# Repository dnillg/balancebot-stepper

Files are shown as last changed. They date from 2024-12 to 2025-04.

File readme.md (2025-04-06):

# Stepper Balance Robot 

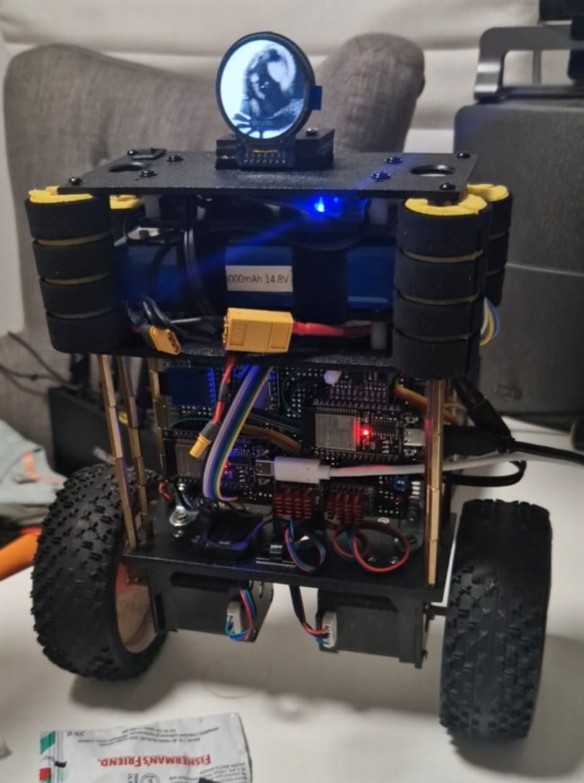
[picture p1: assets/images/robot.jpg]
Robot


## Description
A shoebox sized robot that can balance on two wheels. It uses a PID controller to maintain its balance and can be controlled over Bluetooth via an Android app.
It uses an ESP32 microcontroller, BNO085 IMU, two TMC5160T motor drivers, and two NEMA17 (~1.5A) stepper motors.
The robot is powered by a 3-4S LiPo battery and the chassis consists of metal spacers and 3-4mm PLA sheets.

Apart from the usual components, it has a 240x240 round LCD display and speaker driven by DFPlayer Mini MP3 module.

## Setting up for Development
1. Install VSCode and the PlatformIO extension.
2. Open one of the PlatformIO projects in VSCode (has platformio.ini in root).
3. Install Android Studio
4. Open the client app in Android Studio and run it on your phone.

## Architecture

### Control ESP32
- The ESP32 is the main controller of the robot. 
- It runs the PID controller and communicates with the motor drivers (SPI) and IMU (i2c).
- It has a HardwareSerial connection to the IO-ESP32.
- Control frequency is 200Hz.

### IO ESP32
- The IO ESP32 is responsible for the Bluetooth communication with the Android app.
- It has a HardwareSerial connection to the Control ESP32.
- It is connected to the LCD display (SPI), DFPlayer Mini (Software Serial), SD card module (SPI), and the other ESP32 (Hardware Serial).
- It receives commands from the Android app and sends them to the Control ESP32.
- It also processes the relevant commands.
- It can play sounds and display messages on the LCD with 15+ modes.

## Control / Balance Algorithm
- Cascade PID controller
- The current speed is calculated by the rolling average of the last 500ms
- Speed PID calculates a target roll angle
- Roll PID calculates the target speed of the motors
- The control input applies a difference to the target speed on each motor
- The Stepper motor has a maximum acceleration of ~10000-20000 steps/s², therefore the control output is dampened.
- The control output is limited to 8000 steps/s (Micro stepping: 16)

## Features
- Bluetooth control via Android app
- Diagnostic data streaming and rendering on the app (target roll angle, current roll angle, target speed, current speed, motor speed)
- PID tuning via Android app
- Displaying GIFs on LCD and Sound effects via DFPlayer Mini
- Balancing, driving, and turning

## Planned Features
- Battery feedback and monitoring
- Using a phone game controller Joystick for control

## Bill of Materials
| Component | Quantity | Description |
|---|---|---|
| ESP32 | 2 | 30 pin |
| BNO085 | 1 | IMU |
| TMC5160T | 2 | Motor driver |
| NEMA17 | 2 | Stepper motor, between 1.5A-2.1A nominal current |
| LiPo battery | 1 | 3-4S, 2200-30000mAh |
| LCD | 1 | 240x240 round LCD display |
| Speaker | 1 | 8 ohm, 0.5W-2W |
| DFPlayer Mini | 1 | MP3 module |
| Micro-SD card module | 1 | Micro-SD card module |
| Metal spacer 25mm | 16 | M3 metal spacer for the lower section |
| Metal spacer 20mm | 12 | M3 metal spacer for the upper section |
| 3mm PLA sheet | 2 | 150x65 (2), 35x100 (2) |
| 4mm PLA sheet | 1 | 150x65 |
| NEMA17 mount | 2 | Metal 90 degree bracket for NEMA17 motor |
| M3 screws | ? | 6mm-16mm |
| M3 nuts | ? | M3 nuts |
| Plastic spacer 15mm | 9 | M3 plastic spacer for the upper section |
| 120x80 double PCB | 1 | Double sided prototype PCB |
| XT30 connector | 2 | XT30 connector for power connection |
| XT60 connector | 1 | XT60 connector for power connection |
| 2A 5V DC-DC converter | 1 | DC-DC converter for the ESP32 |
| Pull-down resistor 10k | 1 | 10k pull-down resistor for not-used pins |
| Skotchky diode 1N5819 | 2 | Schottky diode for ESP32 5V in |
| 90 deg. PCB cable connector | 2 | 3pin, 2pin |
| 2 SD cards | 2 | 2x 16GB SD cards |
| 3 pole XT30 connector | 1 | 3 pole XT30 connector for ESP32 5V |
| Bumper foam roll | 4 | 30mm wide Bumper foam for the robot |
| 90 deg mounting bracket for PCB | 4 | 90 deg mounting bracket for PCB |
| 3D Printed 6mm hex to 17MM hex | 2 | 3D printed hex to hex adapter |
| 2 Nitro Buggy wheels | 2 | Nitro buggy wheels for the robot, ca. 110mm diam. | 
| 18AWG copper cable for power connection | 1 | ~ 1-2m |
| 20-wide Jumper wires | 1 | ~ 2-3m |

## Incidents

With limited experience with electronics it's part of the game. :)

### Incident Zero
I used the same connector for the 13V and 5V. I was so excited to test, that I plugged the 5V into the 13V rail.
The ESP32 voltage regulator was glowing and removed itself from the PCB flying with 50-80 cm trajectory.
I was somewhat cautious and did not insert the other components. Luckily.

### First Incident
I tried to debug both ESP32 at the same time via USB, but the 5V and 3.3V rails were connected.
This caused voltage differences and all low voltage components got damaged.
The PCB was also manufactured in a very amateurish way, so I decided to make a new one.

### Second Incident
I made a 3 pole XT30 connector, so I can separate the 5V rails.
I tried to debug the ESP32 via USB, but the 5V rail was still connected. 
I unplugged the wrong connector...

### Component Graveyard

| Component | Quantity | Description |
|---|---|---|
| ESP32 | 1 | Incident Zero |
| ESP32 | 2 | First Incident |
| BNO085 | 1 | First Incident |
| TMC5160T | 2 | First Incident |
| PCB Prototype | 1 | First Incident |
| ESP32 | 1 | Second Incident |

## Pictures
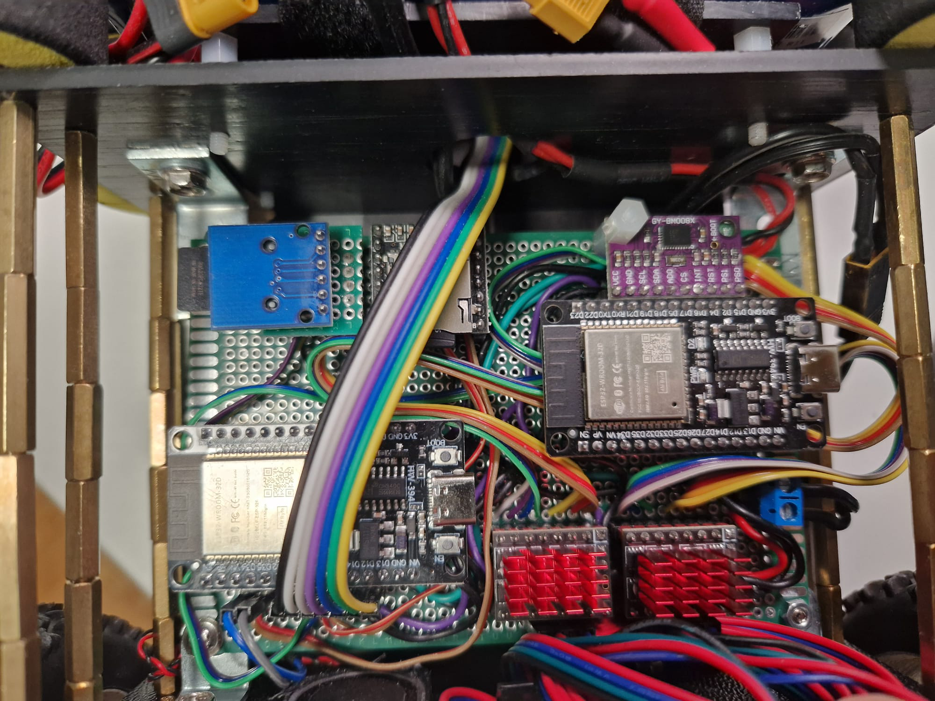
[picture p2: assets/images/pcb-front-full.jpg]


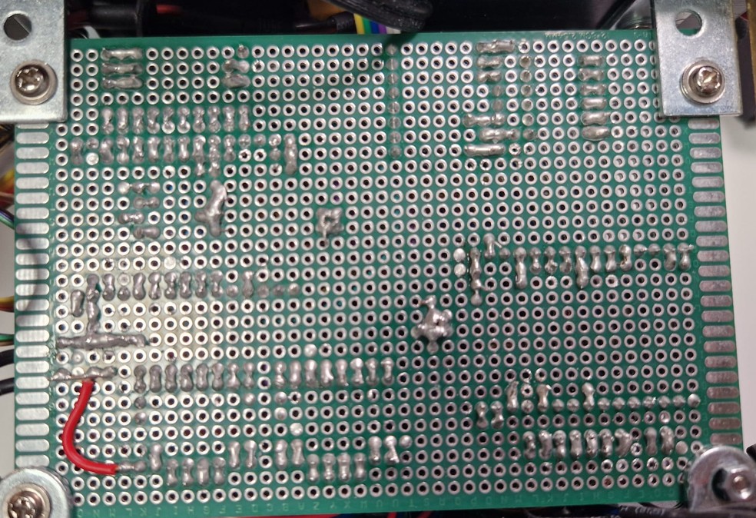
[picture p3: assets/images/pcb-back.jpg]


## History
- I made two robots before with geared DC motors and encoders. (around 2017 and 2019)
- Both could stand, but they were not very stable and could not drive.
- I changed to stepper motors to gain new experience and hoping for better results.
- Over the years I also got maturated and started to do things slower and more carefully.

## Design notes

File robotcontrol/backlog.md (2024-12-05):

#Backlog
- Acceleration limit
- Making sure that it takes the latest IMU value
- PID parameters adjustment remotely
- PID tune

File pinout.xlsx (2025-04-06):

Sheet: Gen1
LEFT TMC5160 | DIR | D22 | SERIAL | D25 | D17
 | STP | D33 |  | D17 | D25
 | CLK | - | DISPLAY | SCL | D18
 | MISO | D19 |  | SDA | D23
 | CS | D21 |  | DC | D5
 | SCK | D18 |  | CS | D16
 | MOSI | D23 |  | RST | D4
 | EN | D32 | MP3 | RX | D19
RIGHT TMC5160 | DIR | D4 |  | TX | D22
 | STP | D16 | CARD | CS | D21 | *
 | CLK |  |  | SCK | D14 | *
 | MISO | D19 |  | MOSI | D13 | *
 | CS | D5 |  | MISO | D12 | *
 | SCK | D18
 | MOSI | D23
 | EN | D26
BNO085 | SCL | D14
 | SDA | D13
 | ADO | -
 | CS | D15
 | INT | D34
 | RST | D27
 | PSI | D2
 | PSO | D12
SERIAL | D25 | D17
 | D17 | D25

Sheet: Gen2
LEFT TMC5160 | DIR | D22 | Gray | SERIAL | Other D16 | D17 | Green
 | STP | D25 | Purple |  | Other D17 | D16 | Blue
 | CLK | GND | Blue | DISPLAY | SCL | D18 | Brown
 | MISO | D19 | Green |  | SDA | D23 | Blue
 | CS | D21 | Yellow |  | DC | D2 | Red
 | SCK | D18 | Orange |  | CS | D5 | Green
 | MOSI | D23 | Red |  | RST | D4 | Purple
 | EN | D32 | Brown | MP3 | RX | D19 | Red
RIGHT TMC5160 | DIR | D4 | Gray |  | TX | D22 | Brown
 | STP | D26 | Purple | CARD | CS | D21 | Yellow
 | CLK | GND | Blue |  | MOSI | D13 | Green
 | MISO | D19 | Green |  | SCK | D14 | Blue
 | CS | D5 | Yellow |  | MISO | D25 | Purple
 | SCK | D18 | Orange
 | MOSI | D23 | Red
 | EN | D33 | Brown
BNO085 | SCL | D14 | Gray
 | SDA (MISO) | D13 | Purple
 | ADO (MOSI?) | GND | Blue
 | CS | D15 | Green
 | INT | D34 | Brown
 | RST | D27 | Red
 | PS0 | D2 | Yellow
 | PS1 | GND | Orange
SERIAL | Other D16 | D17 | Blue
 | Orher D17 | D16 | Green

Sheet: motor-pins
Stepper Online | PIN | Bulkman
Black | A+ | Red
Blue | A- | Blue
Green | B+ | Green
Red | B- | Black

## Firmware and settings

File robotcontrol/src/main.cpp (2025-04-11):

#include <Arduino.h>

#include <HardwareSerial.h>
#include <TMC5160.h>
#include <TMCStepper.h>
#include <AccelStepper.h>
#include <SparkFun_BNO080_Arduino_Library.h>

#include "config.h"
#include "IMU.h"
#include "Motor/Motor.hpp"
#include "SpeedAggregator.hpp"
#include "models/MotorOutput.hpp"
#include "Control.hpp"
#include "MotorOutputFilters/MotorOutputFilter.hpp"
#include "MotorOutputFilters/FailSafe.hpp"
#include "MotorOutputFilters/StationaryCutoff.hpp"
#include "SerialUnits/SerialUnits.hpp"
#include "Motor/MotorPosition.hpp"
#include "Motor/Motors.hpp"
#include "SerialUnits/SerialUnitProcessor.hpp"
#include "Listeners/ControlToggleListener.hpp"
#include "Listeners/RemoteControlListener.hpp"
#include "Listeners/DiagTriggerListener.hpp"
#include "Listeners/GetPidListener.hpp"
#include "Listeners/SetPidListener.hpp"
#include "Listeners/GetConfigListener.hpp"
#include "Listeners/SetConfigListener.hpp"

// ----------------------------------------------------------------------------
// Function Declarations
// ----------------------------------------------------------------------------

// FreeRTOS Tasks
void controlTask(void *pvParameters);
void failsafeTask(void *pvParameters);
void ioSerialReadTask(void *pvParameters);

void halt();

// Timer functions
void IRAM_ATTR motorLeftTimerFunction();
void IRAM_ATTR motorRightTimerFunction();

// Configuration Structures
MotorPins createMotorLeftPins();
MotorPins createMotorRightPins();

// ----------------------------------------------------------------------------
// Global
// ----------------------------------------------------------------------------

struct GlobalState
{
  boolean initialized = false;
  HardwareSerial ioSerial = HardwareSerial(2);
  Control control;
  IMU imu;
  Motor leftMotor = Motor(createMotorLeftPins(), motorLeftTimerFunction, 0, FORWARD, LEFT);
  Motor rightMotor = Motor(createMotorRightPins(), motorRightTimerFunction, 1, BACKWARD, RIGHT);
  Motors motors = Motors(&leftMotor, &rightMotor);
  SpeedAggregator speedAgg500 = SpeedAggregator(10, 10); // 500ms
  SpeedAggregator speedAgg250 = SpeedAggregator(10, 5); // 250ms
  DiagSender diagSender = DiagSender(&ioSerial);
  FailSafeMotorOutputFilter failSafe = FailSafeMotorOutputFilter(FAILSAFE_THRESHOLD_MS);
  StationaryCutoffMotorOutputFilter stationaryCutoff = StationaryCutoffMotorOutputFilter(20, 20, STATIONARY_CUTOFF_ROLL_RANGE, STATIONARY_CUTOFF_SPEED_RANGE);
  MotorOutputFilterChain motorOutputFilterChain = MotorOutputFilterChain();
  RemoteControlListener remoteControlListener = RemoteControlListener(&control);
  ControlToggleListener controlToggleListener = ControlToggleListener(&control, &motors);
  SerialUnitProcessor serialUnitProcessor = SerialUnitProcessor();
  DiagTriggerListener diagTriggerListener = DiagTriggerListener(&diagSender);
  GetPidListener getPidListener = GetPidListener(&control, &ioSerial);
  SetPidListener setPidListener = SetPidListener(&control);
  GetConfigListener getConfigListener = GetConfigListener(&ioSerial, &motors, &control);
  SetConfigListener setConfigListener = SetConfigListener(&ioSerial, &motors, &control);
};

GlobalState gstate;

// ----------------------------------------------------------------------------
// Mutex
// ----------------------------------------------------------------------------

// TODO: Separate mutexes for each motor?
portMUX_TYPE timerMux = portMUX_INITIALIZER_UNLOCKED;

// ----------------------------------------------------------------------------
// Timer Functions
// ----------------------------------------------------------------------------

void IRAM_ATTR motorLeftTimerFunction()
{
  portENTER_CRITICAL_ISR(&timerMux);
  gstate.leftMotor.run();
  portEXIT_CRITICAL_ISR(&timerMux);
}
void IRAM_ATTR motorRightTimerFunction()
{
  portENTER_CRITICAL_ISR(&timerMux);
  gstate.rightMotor.run();
  portEXIT_CRITICAL_ISR(&timerMux);
}

// ----------------------------------------------------------------------------
// Setup
// ----------------------------------------------------------------------------

void setup()
{
  setCpuFrequencyMhz(160);
  delay(50);
  Serial.begin(115200);
  delay(100);

  // Motor Pins
  pinMode(PIN_TMC5160_LEFT_EN, OUTPUT);
  pinMode(PIN_TMC5160_LEFT_STP, OUTPUT);
  pinMode(PIN_TMC5160_LEFT_DIR, OUTPUT);

  pinMode(PIN_TMC5160_RIGHT_EN, OUTPUT);
  pinMode(PIN_TMC5160_RIGHT_STP, OUTPUT);
  pinMode(PIN_TMC5160_RIGHT_DIR, OUTPUT);

  // IMU
  Serial.println("Initializing I2C");
  Wire.begin(PIN_BNO085_SDA, PIN_BNO085_SCL);
  Wire.setClock(400000);
  Serial.println("I2C initialized.");
  if (!gstate.imu.init())
  {
    Serial.println("Could not initialize IMU.");
    halt();
  }
  Serial.println("IMU initialized.");

  Serial.println("Initializing motors");
  gstate.motors.init();
  Serial.println("Motors initialized.");

  Serial.println("Initializing Motor Output Filter Chain");
  if(FAILSAFE_ENABLED) {
    gstate.motorOutputFilterChain.add(&gstate.failSafe);
  }
  gstate.motorOutputFilterChain.add(&gstate.stationaryCutoff);
  Serial.println("Motor Output Filter Chain initialized.");

  if (ENABLE_CONTROL_ON_STARTUP) {
    gstate.motors.enable();
    Serial.println("Motors enabled.");
    gstate.control.enable();
    Serial.println("Control enabled.");
  } else {
    gstate.motors.disable();
    Serial.println("Motors disabled.");
    gstate.control.disable();
    Serial.println("Control disabled.");  
  }

  gstate.serialUnitProcessor.addListener(&gstate.remoteControlListener);
  gstate.serialUnitProcessor.addListener(&gstate.controlToggleListener);
  gstate.serialUnitProcessor.addListener(&gstate.diagTriggerListener);
  gstate.serialUnitProcessor.addListener(&gstate.getPidListener);
  gstate.serialUnitProcessor.addListener(&gstate.setPidListener);
  gstate.serialUnitProcessor.addListener(&gstate.getConfigListener);
  gstate.serialUnitProcessor.addListener(&gstate.setConfigListener);

  #if IO_SERIAL_ENABLED == true
  Serial.println("Initializing IO Serial");
  gstate.ioSerial.begin(IO_SERIAL_BAUD);
  delay(100);
  Serial.println("IO Serial initialized.");
  #endif

  #if CONTROL_TASK_ENABLED == true
  xTaskCreatePinnedToCore(
      controlTask,
      "ctrl",
      4096,
      NULL,
      2,
      NULL,
      1);
  Serial.println("ControlTask started.");
  #endif

  #if IO_SERIAL_ENABLED == true
  Serial.println("Initializing IO Serial Task");  
  xTaskCreatePinnedToCore(
      ioSerialReadTask,
      "ioSerial",
      4096,
      NULL,
      4,
      NULL,
      0);
  Serial.println("IO Serial Task started.");
  #endif

  gstate.initialized = true;
  Serial.println("Initialization complete.");
}

void ioSerialReadTask(void *pvParameters)
{
  while (true)
  {
    if (gstate.ioSerial.available()) {
      String input = gstate.ioSerial.readStringUntil('\n');
      gstate.serialUnitProcessor.process(SerialUnitFactory::readAlias(input), input);
    }
    vTaskDelay(1 / portTICK_PERIOD_MS);
  }
}

void controlTask(void *pvParameters)
{
  const TickType_t xFrequency = pdMS_TO_TICKS(1000 / CONTROL_FREQUENCY); // 5 ms = 200 Hz
  while (true)
  {
    TickType_t xLastWakeTime = xTaskGetTickCount();
    gstate.serialUnitProcessor.run();
    if (gstate.initialized)
    {
      gstate.imu.getData();
      float currentRoll = gstate.imu.getRoll();
      
      gstate.failSafe.setRoll(currentRoll);
      gstate.control.setInputAngleRad(currentRoll);
      gstate.control.setInputSpeedAvg250(gstate.speedAgg250.getSpeed());
      gstate.control.setInputSpeedAvg500(gstate.speedAgg500.getSpeed());

      gstate.control.compute();

      uint16_t cycleNo = gstate.control.getCycleNo();

      int16_t step16SpeedLeft = gstate.control.getSteps16Left();
      int16_t step16SpeedRight = gstate.control.getSteps16Right();

      int16_t filteredStep16SpeedLeft = gstate.motorOutputFilterChain.filter(step16SpeedLeft, LEFT);
      int16_t filteredStep16SpeedRight = gstate.motorOutputFilterChain.filter(step16SpeedRight, RIGHT);
      
      gstate.leftMotor.setSpeed(-filteredStep16SpeedLeft); 
      gstate.rightMotor.setSpeed(-filteredStep16SpeedRight);

      int16_t controlSpeed = (((int32_t)step16SpeedLeft) + step16SpeedRight) / 2;
      gstate.stationaryCutoff.consumeRollAndMotorSpeed(currentRoll, controlSpeed);
      gstate.speedAgg500.consume(controlSpeed);
      gstate.speedAgg250.consume(controlSpeed);

      DiagDTO dto = DiagDTO();
      dto.cycleNo = cycleNo;
      dto.millis = gstate.control.getMillis();
      dto.roll = currentRoll;
      dto.rollSetpoint = gstate.control.getRollSetpoint();
      dto.speed = gstate.speedAgg500.getSpeed();
      dto.speedSetpoint = gstate.control.getInput().step16SpeedSetpoint;
      dto.steerOffset = gstate.control.getInput().steerOffset;
      dto.step16SpeedLeft = step16SpeedLeft;
      dto.step16SpeedRight = step16SpeedRight;
      gstate.diagSender.send(dto);

      // if (dto.cycleNo % 8 == 0) {
      //   Serial.println(gstate.speedAgg500.getSpeed());
      // }

      gstate.failSafe.heartBeat();
    }

    vTaskDelayUntil(&xLastWakeTime, xFrequency);
  }
}

void halt()
{
  while (true)
  {
    delay(1000);
  }
}

MotorPins createMotorLeftPins()
{
  MotorPins motorPins;
  motorPins.dir = PIN_TMC5160_LEFT_DIR;
  motorPins.stp = PIN_TMC5160_LEFT_STP;
  motorPins.clk = PIN_TMC5160_LEFT_CLK;
  motorPins.miso = PIN_TMC5160_LEFT_MISO;
  motorPins.cs = PIN_TMC5160_LEFT_CS;
  motorPins.sck = PIN_TMC5160_LEFT_SCK;
  motorPins.mosi = PIN_TMC5160_LEFT_MOSI;
  motorPins.en = PIN_TMC5160_LEFT_EN;
  return motorPins;
}

MotorPins createMotorRightPins()
{
  MotorPins motorPins;
  motorPins.dir = PIN_TMC5160_RIGHT_DIR;
  motorPins.stp = PIN_TMC5160_RIGHT_STP;
  motorPins.clk = PIN_TMC5160_RIGHT_CLK;
  motorPins.miso = PIN_TMC5160_RIGHT_MISO;
  motorPins.cs = PIN_TMC5160_RIGHT_CS;
  motorPins.sck = PIN_TMC5160_RIGHT_SCK;
  motorPins.mosi = PIN_TMC5160_RIGHT_MOSI;
  motorPins.en = PIN_TMC5160_RIGHT_EN;
  return motorPins;
}

void loop()
{
  // Empty loop, all tasks are handled in FreeRTOS tasks
}

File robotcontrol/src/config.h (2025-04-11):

// my_class.h
#ifndef CONFIG_H // include guard
#define CONFIG_H

// ----------------------------------------------------------------------------
// Logging
// ----------------------------------------------------------------------------

#define PRINT_CONTROL_STATE false

// ----------------------------------------------------------------------------
// Motor Config
// ----------------------------------------------------------------------------

#define MOTOR_R_SENSE 0.075f
#define MOTOR_TOFF 5
#define MOTOR_RMS_CURRENT 1500
#define MOTOR_IRUN 26
#define MOTOR_IHOLD 18
#define MOTOR_IHOLDDELAY 5
#define MOTOR_MAX_MICROSTEPPING 16
#define MOTOR_PWM_AUTOSCALE true
#define MOTOR_PWM_MODE true

#define MOTOR_MAX_SPEED 10000
#define MOTOR_MAX_ACCELERATION 12000

// ----------------------------------------------------------------------------
// IO Serial Config
// ----------------------------------------------------------------------------

#define IO_SERIAL_BAUD 115200
#define IO_SERIAL_PORT 2
#define IO_SERIAL_ENABLED true

// ----------------------------------------------------------------------------
// IMU Config
// ----------------------------------------------------------------------------

#define BNO085_I2C_ADDR 0x4B
#define BNO085_ROTATION_VECTOR_PERIOD 5 // 5ms = 200Hz

// ----------------------------------------------------------------------------
// BALANANCE CONTROL
// ----------------------------------------------------------------------------
#define FAILSAFE_ENABLED true
#define FAILSAFE_THRESHOLD_MS 100
#define FAILSAFE_MAX_ROLL_OFFSET 0.9

#define CONTROL_DRY_RUN false
#define CONTROL_TASK_ENABLED true
#define ENABLE_CONTROL_ON_STARTUP false
#define CONTROL_FREQUENCY 200

#define CONTROL_TARGET_ROLL -1.495
#define CONTROL_MAX_TARGET_STEP16_SPEED 2800
#define CONTROL_MAX_SPEED_ROLL_RAD_OFFSET 0.75 // 40-45 degrees in radians
#define CONTROL_MAX_STEER_STEP16_OFFSET 3200

#define CONTROL_ROLL_PID_KP 44300
#define CONTROL_ROLL_PID_KI 5000
#define CONTROL_ROLL_PID_KD 94

#define CONTROL_SPEED_PID_KP 0.000045
#define CONTROL_SPEED_PID_KI 0.0
#define CONTROL_SPEED_PID_KD 0.0015

#define CONTROL_MAX_STEP16_SPEED 10000
#define CONTROL_MAX_ACCELERATION 40000

#define CONTROL_MAX_SPEED_PID_OUTPUT_ACCELERATION 2 // Might be not needed

#define STATIONARY_CUTOFF_ENABLED true
#define STATIONARY_CUTOFF_SPEED_RANGE 200.0
#define STATIONARY_CUTOFF_ROLL_RANGE 0.0065

// ----------------------------------------------------------------------------
// Pins
// ----------------------------------------------------------------------------

#define PIN_TMC5160_LEFT_DIR 22
#define PIN_TMC5160_LEFT_STP 25
#define PIN_TMC5160_LEFT_CLK -1
#define PIN_TMC5160_LEFT_MISO 19
#define PIN_TMC5160_LEFT_CS 21
#define PIN_TMC5160_LEFT_SCK 18
#define PIN_TMC5160_LEFT_MOSI 23
#define PIN_TMC5160_LEFT_EN 32

#define PIN_TMC5160_RIGHT_DIR 4
#define PIN_TMC5160_RIGHT_STP 26
#define PIN_TMC5160_RIGHT_CLK -1
#define PIN_TMC5160_RIGHT_MISO 19
#define PIN_TMC5160_RIGHT_CS 5
#define PIN_TMC5160_RIGHT_SCK 18
#define PIN_TMC5160_RIGHT_MOSI 23
#define PIN_TMC5160_RIGHT_EN 33

#define PIN_BNO085_SCL 14
#define PIN_BNO085_SDA 13
#define PIN_BNO085_ADO -1
#define PIN_BNO085_CS 15
#define PIN_BNO085_INT 34
#define PIN_BNO085_RST 27
#define PIN_BNO085_PSO 2
#define PIN_BNO085_PSI -1

#define PIN_SERIAL_RX 17
#define PIN_SERIAL_TX 16

#endif /* CONFIG_H */

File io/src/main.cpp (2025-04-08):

#include <Wire.h>
#include <Arduino.h>
#include <BluetoothSerial.h>
#include <SoftwareSerial.h>
#include <SD.h>
#include <SPI.h>
#include <TFT_eSPI.h>
#include <AnimatedGIF.h>
#include <DFPlayer.h>
#include <DFMiniMp3.h>

#include "DfConfig.h"
#include "config.h"
#include "SerialUnits/SerialUnitProcessor.hpp"
#include "Soul.hpp"
#include "Listeners/SequenceTriggerListener.hpp"
#include "esp_system.h"
#include "esp_err.h"
#include "BluetoothSentinel.hpp"
//#include <WiFi.h>

// ----------------------------------------------------------------------------
// Function Declarations
// ----------------------------------------------------------------------------

void halt();

// Tasks
void bluetoothSerialReaderTask(void *pvParameters);
void controlSerialReaderTask(void *pvParameters);
void runnerTask(void *pvParameters);
void bluetoothSentinelTask(void *pvParameters);

// ----------------------------------------------------------------------------
// Global Variables
// ----------------------------------------------------------------------------

struct GlobalState
{
  HardwareSerial controlSerial;
  BluetoothSerial serialBT;

  SerialUnitProcessor serialUnitProcessor;
  EspSoftwareSerial::UART mp3Serial;
  TFT_eSPI tft;
  RobotDisplay display;
  Soul soul;
  DfMp3 dfplayer;
  BluetoothSentinel btSentinel;

  GlobalState()
      : controlSerial(2),
        serialBT(),
        serialUnitProcessor(),
        tft(TFT_eSPI(240, 240)),
        mp3Serial(PIN_MP3_SERIAL_RX, PIN_MP3_SERIAL_TX),
        display(tft),
        dfplayer(mp3Serial),
        soul(&dfplayer, &display),
        btSentinel(serialBT, serialUnitProcessor, controlSerial)
  {
  }
};
GlobalState gstate;

// ----------------------------------------------------------------------------
// Setup
// ----------------------------------------------------------------------------

SPIClass SPISD(HSPI);
SPIClass SPITFT(VSPI);

void setup()
{
  setCpuFrequencyMhz(160);
  delay(10);
  // esp_log_level_set("*", ESP_LOG_INFO);  // Set log level for verbosity
  delay(10);
  //WiFi.mode(WIFI_OFF);  

  gstate.controlSerial.begin(CONTROL_SERIAL_BAUD);
  Serial.begin(SERIAL_BAUD);
  if (!gstate.serialBT.begin(BLUETOOTH_NAME))
  {
    Serial.println("FATAL_ERROR: Failed to initialize Bluetooth!");
    halt();
  }
  Serial.println("Bluetooth device started, ready to pair with name: " + String(BLUETOOTH_NAME));

  SPISD.begin(PIN_CARD_SCK, PIN_CARD_MISO, PIN_CARD_MOSI, PIN_CARD_CS);
  Serial.println("HSPI (Card) initialized");
  if (!SD.begin(PIN_CARD_CS, SPISD, 4000000))
  {
    Serial.println("ERROR: SD card initialization failed!");
    return;
  }
  Serial.println("SD card initialized.");

  Serial.println("Initializing DFPlayer.");
  gstate.mp3Serial.begin(9600, EspSoftwareSerial::SWSERIAL_8N1, PIN_MP3_SERIAL_RX, PIN_MP3_SERIAL_TX);
  delay(100);
  gstate.dfplayer.begin();
  gstate.dfplayer.reset(); 
  gstate.dfplayer.setPlaybackSource(DfMp3_PlaySource_Sd);
  gstate.dfplayer.setPlaybackMode(DfMp3_PlaybackMode::DfMp3_PlaybackMode_Repeat);
  gstate.dfplayer.setVolume(12);
  Serial.println("DFPlayer initialized.");

  gstate.tft.init();
  Serial.println("TFT initialized");

  gstate.tft.fillScreen(TFT_BLACK);
  gstate.tft.setSwapBytes(true);

  gstate.serialUnitProcessor.addListener(new SequenceTriggerListener(&gstate.soul));
  gstate.soul.setSequence(SequenceType::WINXP_START);

  xTaskCreatePinnedToCore(
      bluetoothSerialReaderTask,
      "bluetoothSerial",
      4096,
      NULL,
      6,
      NULL,
      1);

  xTaskCreatePinnedToCore(
      controlSerialReaderTask,
      "controlSerial",
      4096,
      NULL,
      6,
      NULL,
      1);

  xTaskCreatePinnedToCore(
      runnerTask,
      "executor",
      6096,
      NULL,
      2,
      NULL,
      1);

  xTaskCreatePinnedToCore(
      bluetoothSentinelTask,
      "bluetoothSentinel",
      2048,
      NULL,
      4,
      NULL,
      1);

  Serial.println("Setup complete.");
}

// ----------------------------------------------------------------------------
// Loop
// ----------------------------------------------------------------------------

void loop()
{
  // Nothing to do here, everything is handled in tasks
}

// ----------------------------------------------------------------------------
// Function Definitions
// ----------------------------------------------------------------------------

void processSerialUnit(SerialUnitEndpoint source, String &line)
{
  SerialUnitAlias alias = SerialUnitFactory::readAlias(line);
  gstate.serialUnitProcessor.process(alias, line);
}

void halt()
{
  while (true)
  {
    Serial.println("Halting...");
    delay(1000);
  }
}

// ----------------------------------------------------------------------------
// Task Definitions
// ----------------------------------------------------------------------------

void bluetoothSerialReaderTask(void *pvParameters)
{
  while (true)
  {
    while (gstate.serialBT.available())
    {
      try {
        // TODO: Make a very effective buffering for the current line and sending to the controlSerial
        String line = gstate.serialBT.readStringUntil('\n');
        gstate.controlSerial.println(line);
        gstate.controlSerial.flush();
        processSerialUnit(BLUETOOTH, line);
        // Serial.print("BT-REC: ");
        // Serial.println(line);
      } catch (const std::exception& e) {
        Serial.println("ERROR: Could not read bluetooth serial. Reason: " + String(e.what()));
      }
    }
    vTaskDelay(portTICK_PERIOD_MS);
  }
}

void controlSerialReaderTask(void *pvParameters)
{
  uint8_t buffer[64];
  while (true)
  {
    while (gstate.controlSerial.available())
    {
      //String line = gstate.controlSerial.readStringUntil('\n');
      //processSerialUnit(CONTROL, line);
      size_t read = gstate.controlSerial.readBytes(buffer, 64);
      gstate.serialBT.write(buffer, read);
    }
    vTaskDelay(portTICK_PERIOD_MS);
  }
}

void runnerTask(void *pvParameters)
{
  while (true)
  {
    gstate.serialUnitProcessor.run();
    gstate.soul.run();
    gstate.display.run();
    gstate.dfplayer.loop();
    taskYIELD(); // Does not delay, but allows other tasks to run
  }
}

void bluetoothSentinelTask(void *pvParameters)
{
  while (true) {
    gstate.btSentinel.run();
    vTaskDelay(100 / portTICK_PERIOD_MS);
  }
}

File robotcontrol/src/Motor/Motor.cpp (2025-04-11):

#include "Motor.hpp"

Motor::Motor(MotorPins pins, void (*timerFunction)(void), uint8_t timerIdx, Direction direction, MotorPosition motorPos) : driver(pins.cs, MOTOR_R_SENSE, pins.mosi, pins.miso, pins.sck),
                                                                                                                           stepper(1, pins.stp, pins.dir),
                                                                                                                           position(motorPos)
{
  this->enablePin = pins.en;
  this->timerFunction = timerFunction;
  this->stepTimer = timerBegin(timerIdx, 80, true); // 80 cycles: 1us, TODO: check if this is correct
  this->direction = direction;
}

void Motor::init(const TMC5160Config& config)
{
  driver.begin();
  driver.microsteps(MOTOR_MAX_MICROSTEPPING);
  stepper.setPinsInverted(direction == BACKWARD, false, true);
  applyConfig(config);
  timerAttachInterrupt(this->stepTimer, timerFunction, true);
  timerAlarmWrite(this->stepTimer, 1000, true); // 1000: 1ms
  timerAlarmEnable(this->stepTimer);
}

void Motor::applyConfig(const TMC5160Config& config)
{
  //  TOFF: 3-5 recommended, 0-15
  //  high: stable, lower power, low: noisy
  driver.toff(config.toff);
  driver.rms_current(config.rms_current);
  driver.irun(config.irun);
  driver.ihold(config.ihold);
  driver.iholddelay(config.iholddelay);
  // driver.TCOOLTHRS(0);
  // driver.TPWMTHRS(500);
  // driver.THIGH(500);

  driver.pwm_autoscale(config.pwm_autoscale);

  driver.en_pwm_mode(config.pwm_mode); // Toggle stealthChop

  stepper.setMaxSpeed(config.max_speed);
  stepper.setAcceleration(config.max_acceleration);
}

void Motor::setSpeed(int16_t speed)
{
  if (speed == stepper.speed())
  {
    return;
  }

  stepper.setSpeed(speed);
  if (speed == 0)
  {
    timerAlarmWrite(stepTimer, 1000, true); // 1ms
    return;
  }
  // Adjusting the timer according to the new speed
  uint32_t ticks = 1000000;
  ticks /= abs(speed);
  ticks /= 10; // Triggering 10 times per step
  if (ticks < 66)
  {
    ticks = 66;
  }
  timerAlarmWrite(stepTimer, ticks, true);
}

void Motor::disable()
{
  digitalWrite(enablePin, HIGH);
}

void Motor::enable()
{
  if (!CONTROL_DRY_RUN)
  {
    digitalWrite(enablePin, LOW);
  }
}

uint32_t Motor::getStatus()
{
  return driver.DRV_STATUS();
}

uint8_t Motor::getEncStatus()
{
  driver.ENC_STATUS();
}

void Motor::logStatus()
{
  Serial.print("SG_RESULT: ");
  Serial.println(driver.sg_result());

  Serial.print("FS_ACTIVE: ");
  Serial.println(driver.fsactive());

  Serial.print("CS_ACTUAL: ");
  Serial.println(driver.cs_actual());

  Serial.print("STALLGUARD: ");
  Serial.println(driver.stallguard());

  Serial.print("Overtemp (OT): ");
  Serial.println(driver.ot());

  Serial.print("Overtemp Warning (OTPW): ");
  Serial.println(driver.otpw());

  Serial.print("Short to Ground A (S2GA): ");
  Serial.println(driver.s2ga());

  Serial.print("Short to Ground B (S2GB): ");
  Serial.println(driver.s2gb());

  Serial.print("Open Load A (OLA): ");
  Serial.println(driver.ola());

  Serial.print("Open Load B (OLB): ");
  Serial.println(driver.olb());

  Serial.print("Standstill (STST): ");
  Serial.println(driver.stst());
}

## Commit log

2024-12-05 Speed works, dampener, stable pid
2024-12-07 good balance, cascade pid
2024-12-16 Android app
    [pinout.xlsx]
2024-12-21 Pid Adjustment 1
2024-12-22 IO project
    [pinout.xlsx]
2024-12-26 Serial bridge ok, animation plays, Mp3 is meh
    [pinout.xlsx]
2025-03-26 Media switch works
2025-04-05 Tidying up the repo
    [pcb.kicad_pcb, pcb.kicad_sch]
2025-04-06 GetPid, SetPid Works
    [pinout.xlsx]
